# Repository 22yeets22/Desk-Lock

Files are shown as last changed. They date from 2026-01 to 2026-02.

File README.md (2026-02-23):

# Desk-Lock

A cheap desk lock that unlocks with an NFC card.

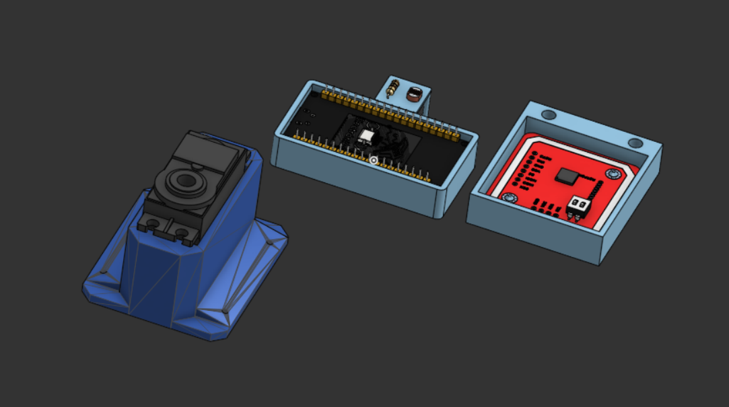
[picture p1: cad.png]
Desk Lock

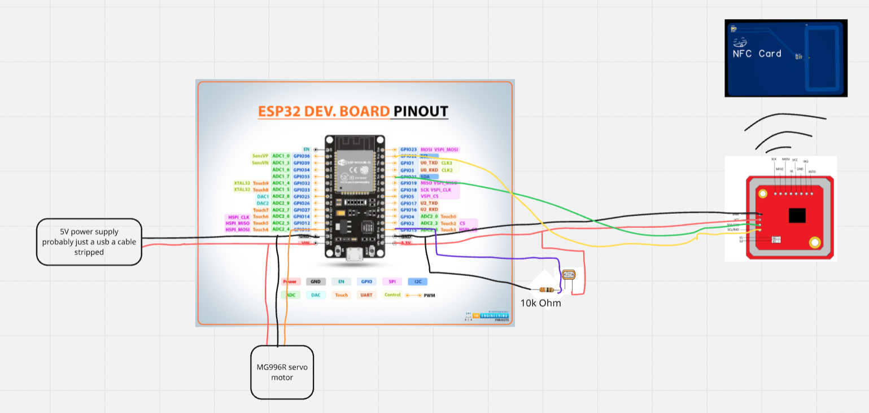
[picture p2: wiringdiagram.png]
Wiring Diagram


## Overview

This project is a DIY desk lock which keeps items in your desk secure by using a NFC reader. An ESP32 reads an NFC card via a PN532 module and controls a servo motor that locks or unlocks the desk. A photoresistor is used to detect when the drawer is closed so it can relock automatically.

[Detailed Description Here](#Detailed-Description)

## Motivation

I wanted a secure way to lock my desk because I keep important items inside and my little brother cannot be trusted with it. Buying a commercial lock felt boring and expensive, so building one with NFC was more interesting and let me design my own NFC card and reader.

## Parts List (Bill of Materials)

- 1x of [Photoresistor](https://www.aliexpress.us/item/3256805782399608.html), TYPE 5528, PRICE $2.39
- 1x of [10k Resistor](https://www.aliexpress.us/item/2251832766343175.html), TYPE 10K, PRICE $1.25
- 1x of [MG996R Servo](https://www.aliexpress.us/item/3256808293405785.html), TYPE N/A, PRICE $0.99
- 1x of [AC to DC Power Supply](https://www.aliexpress.us/item/3256806901002886.html), TYPE US Plug/DC 5V/4A, PRICE $4.60
- 1x of [ESP32 Development Board](https://www.aliexpress.us/item/3256805767190776.html), TYPE 1PCS-CP2102 TYPE-C, PRICE $6.56
- 1x of [PN532 NFC Module](https://www.aliexpress.us/item/3256806852006648.html), TYPE PN532, PRICE $3.67

### NFC Card - 25.33 for 5

| Schematic | PCB | 3D View |
| --- | --- | --- |
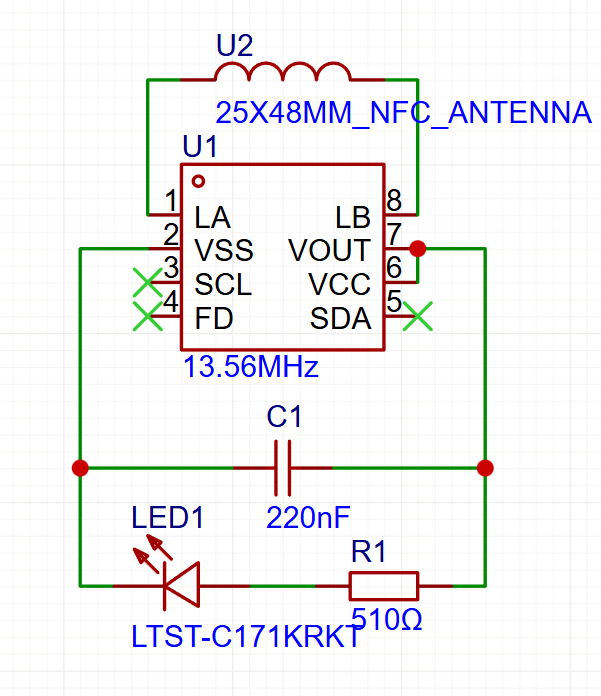
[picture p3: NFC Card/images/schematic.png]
Schematic
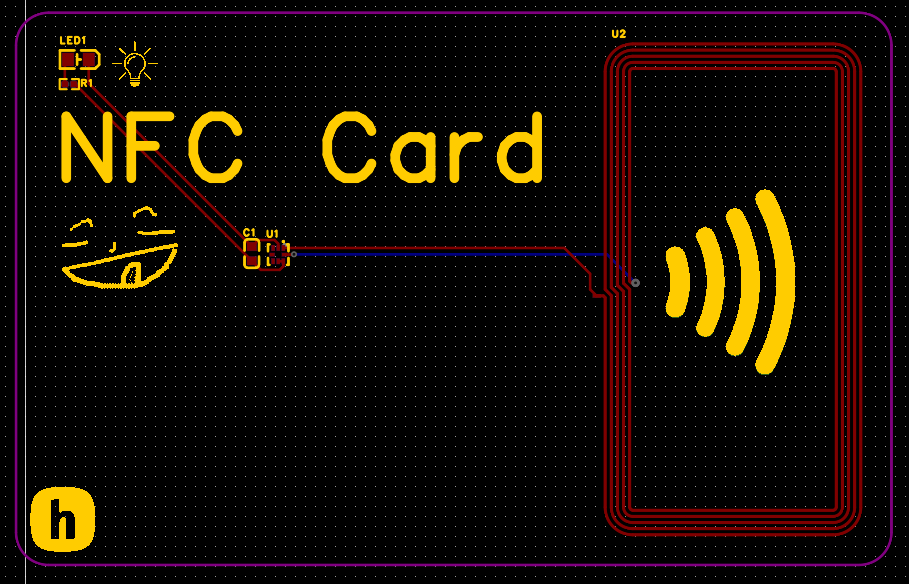
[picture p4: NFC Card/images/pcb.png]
PCB
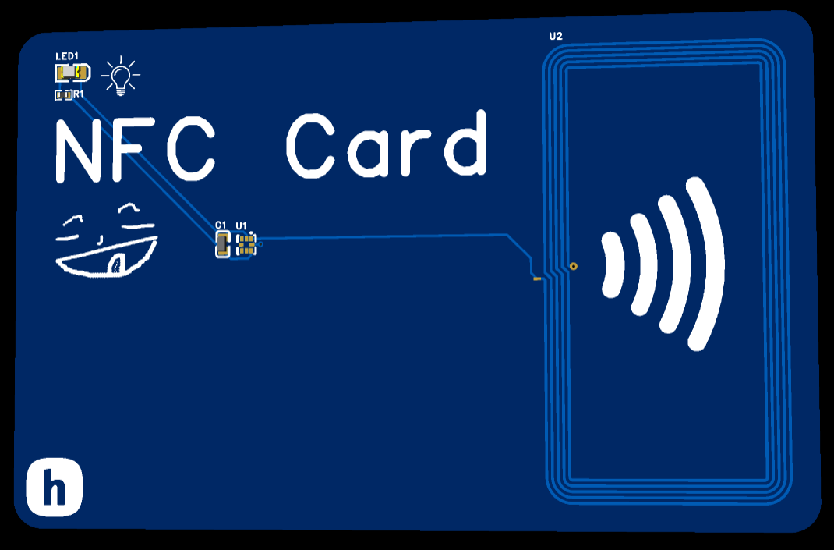
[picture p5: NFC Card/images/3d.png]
3D
|  |  |  |

## Detailed Description

This project is a DIY NFC-based desk lock using an ESP32. A PN532 NFC reader communicates with the ESP32 over I2C to read NFC cards. When an authorized card is detected, the ESP32 drives a servo motor to unlock the drawer. Unauthorized cards are ignored.<br>
The servo is powered by an external supply that also powers the ESP32 and is mounted so one position locks the drawer and another unlocks it. The mechanical design is flexible and can support different desk types.<br>
A photoresistor inside the drawer is wired as a voltage divider with a 10 kΩ resistor and connected to an ESP32 ADC pin. It detects whether the drawer is open or closed based on light level. After unlocking, the system waits until the drawer is closed (becomes dark), then automatically relocks after a configurable delay (default 10 seconds).

## CAD

There is a case for every single part in this project:

- ESP32 Case: for the esp32 (duh)
- PHotoresistor Case: for the photoresistor + resistor setup to detect desk drawer close
- MG996R Case: Servo case for a wider base which improves adhesion + screw holes if you need it
- PN532 Case (Case + Lid): Case + lid for the nfc reader module
- And also, a full assembly with all electronics included!

## Example Placement Diagram

Here is an example placement diagram for the servo:


## Notes

The servo holder was not made by me, but suits the purpose perfectly.

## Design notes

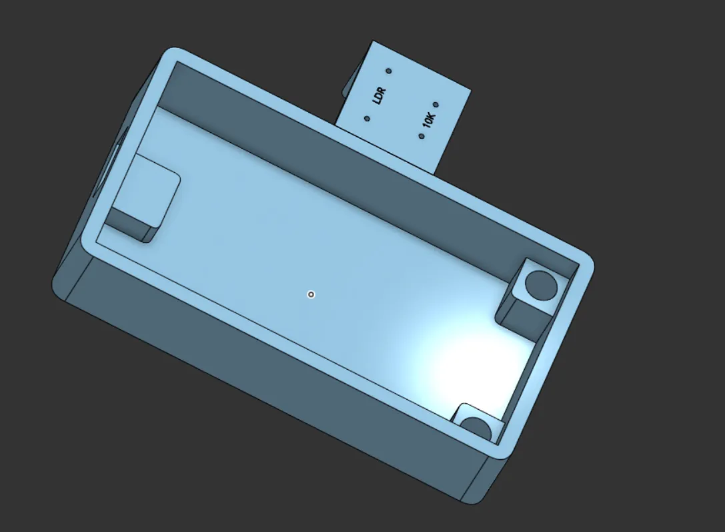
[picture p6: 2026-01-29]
3d.png

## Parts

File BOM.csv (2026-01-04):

Part | Type | Quantity | Unit Price | Link
Photoresistor | 5528 | 1 | 2.39 | https://www.aliexpress.com/item/3256805782399608.html
10k Resistor | 10K | 1 | 1.25 | https://www.aliexpress.com/item/2251832766343175.html
MG996R Servo | N/A | 1 | 0.99 | https://www.aliexpress.com/item/3256808293405785.html
AC to DC Power Supply | US Plug/DC 5V/4A | 1 | 4.60 | https://www.aliexpress.com/item/3256806901002886.html
ESP32 Dev Board | 1PCS-CP2102 TYPE-C | 1 | 6.56 | https://www.aliexpress.com/item/3256805767190776.html
PN532 NFC Module | PN532 | 1 | 3.67 | https://www.aliexpress.com/item/3256806852006648.html
CUSTOM NFC CARD | N/A | 5 | 25.33 | https://github.com/22yeets22/Desk-Lock/tree/main/NFC%20Card

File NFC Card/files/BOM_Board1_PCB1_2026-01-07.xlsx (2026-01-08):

No. | Quantity | Comment | Designator | Footprint | Value | Manufacturer Part | Manufacturer | Supplier Part | Supplier
1 | 1 | 220nF | C1 | C0603 | 220nF | CL10B224KA8NNNC | SAMSUNG(三星) | C21120 | LCSC
2 | 1 | LTST-C171KRKT | LED1 | LED-SMD_L2.0-W1.25-RD_RED |  | LTST-C171KRKT | LITEON(光宝) | C284871 | LCSC
3 | 1 | 510Ω | R1 | R0402 | 510Ω | RC0402FR-07510RL | YAGEO(国巨) | C276273 | LCSC
4 | 1 | 13.56MHz | U1 | XQFN-8_L1.6-W1.6-P0.50-BL_NT3H2111W0FHKH | 13.56MHz | NT3H2111W0FHKH | NXP(恩智浦) | C710403 | LCSC
5 | 1 | 25X48MM_NFC_ANTENNA | U2 | 25X48MM_NFC_ANTENNA

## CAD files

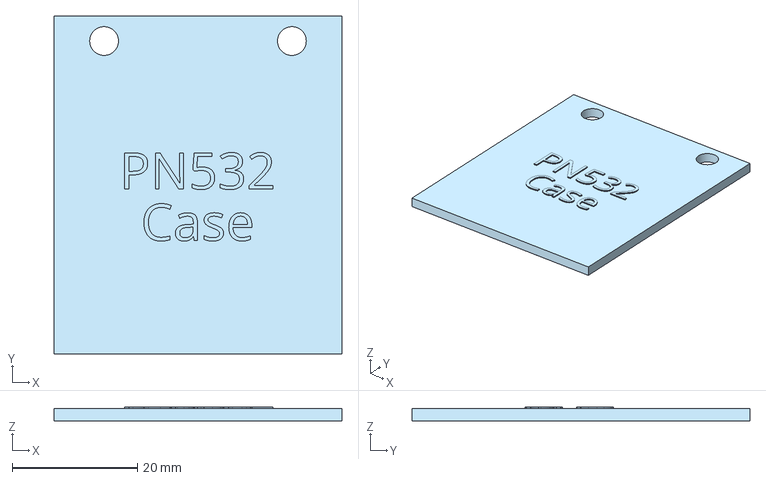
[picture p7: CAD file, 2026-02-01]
CAD/PN532 Case Lid.step
46.0 x 54.0 x 2.20 mm

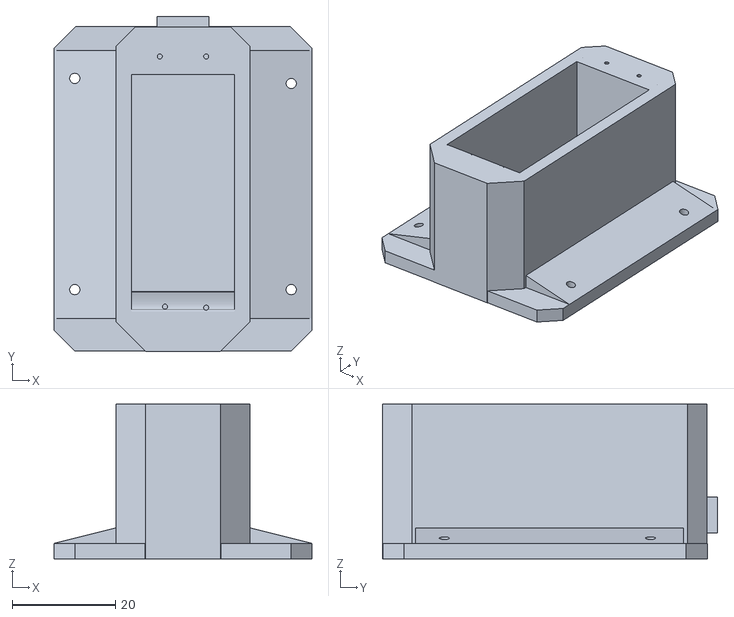
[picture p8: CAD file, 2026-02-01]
CAD/MG996R Case.stl
50.0 x 65.0 x 30.0

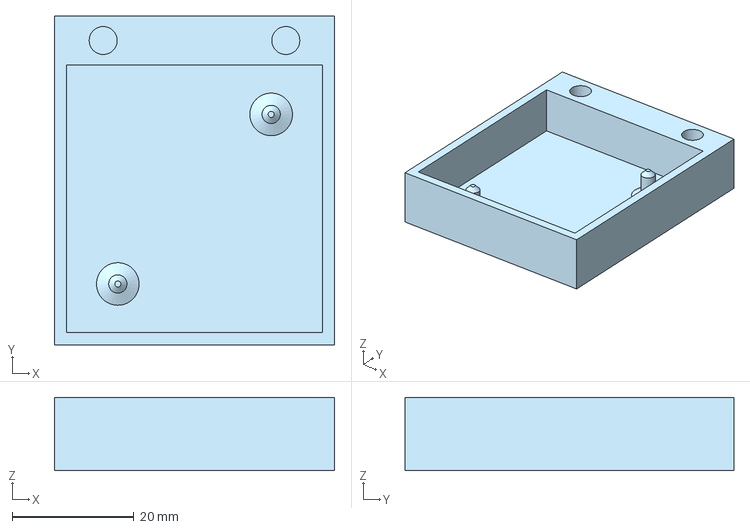
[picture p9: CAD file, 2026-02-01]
CAD/PN532 Case.step
46.0 x 54.0 x 12.0 mm

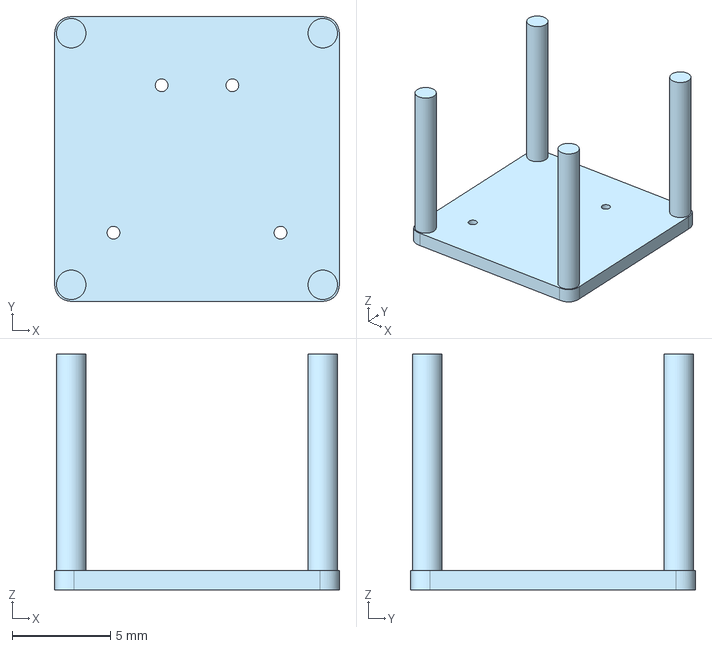
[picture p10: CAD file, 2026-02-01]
CAD/Photoresistor Case.step
14.5 x 14.5 x 12.0 mm

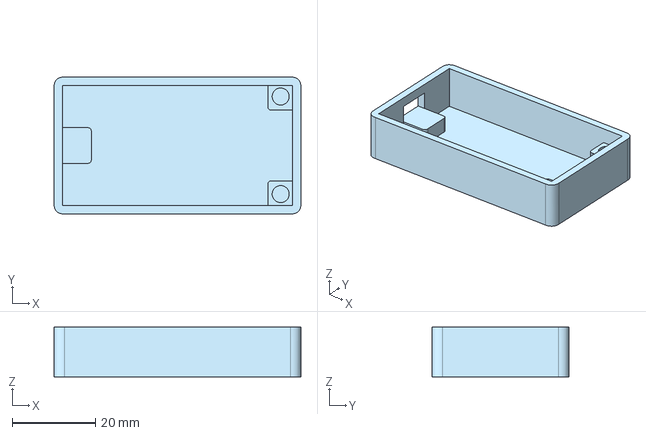
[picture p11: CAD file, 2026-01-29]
CAD/ESP32 Case.step
59.5 x 33.0 x 12.0 mm

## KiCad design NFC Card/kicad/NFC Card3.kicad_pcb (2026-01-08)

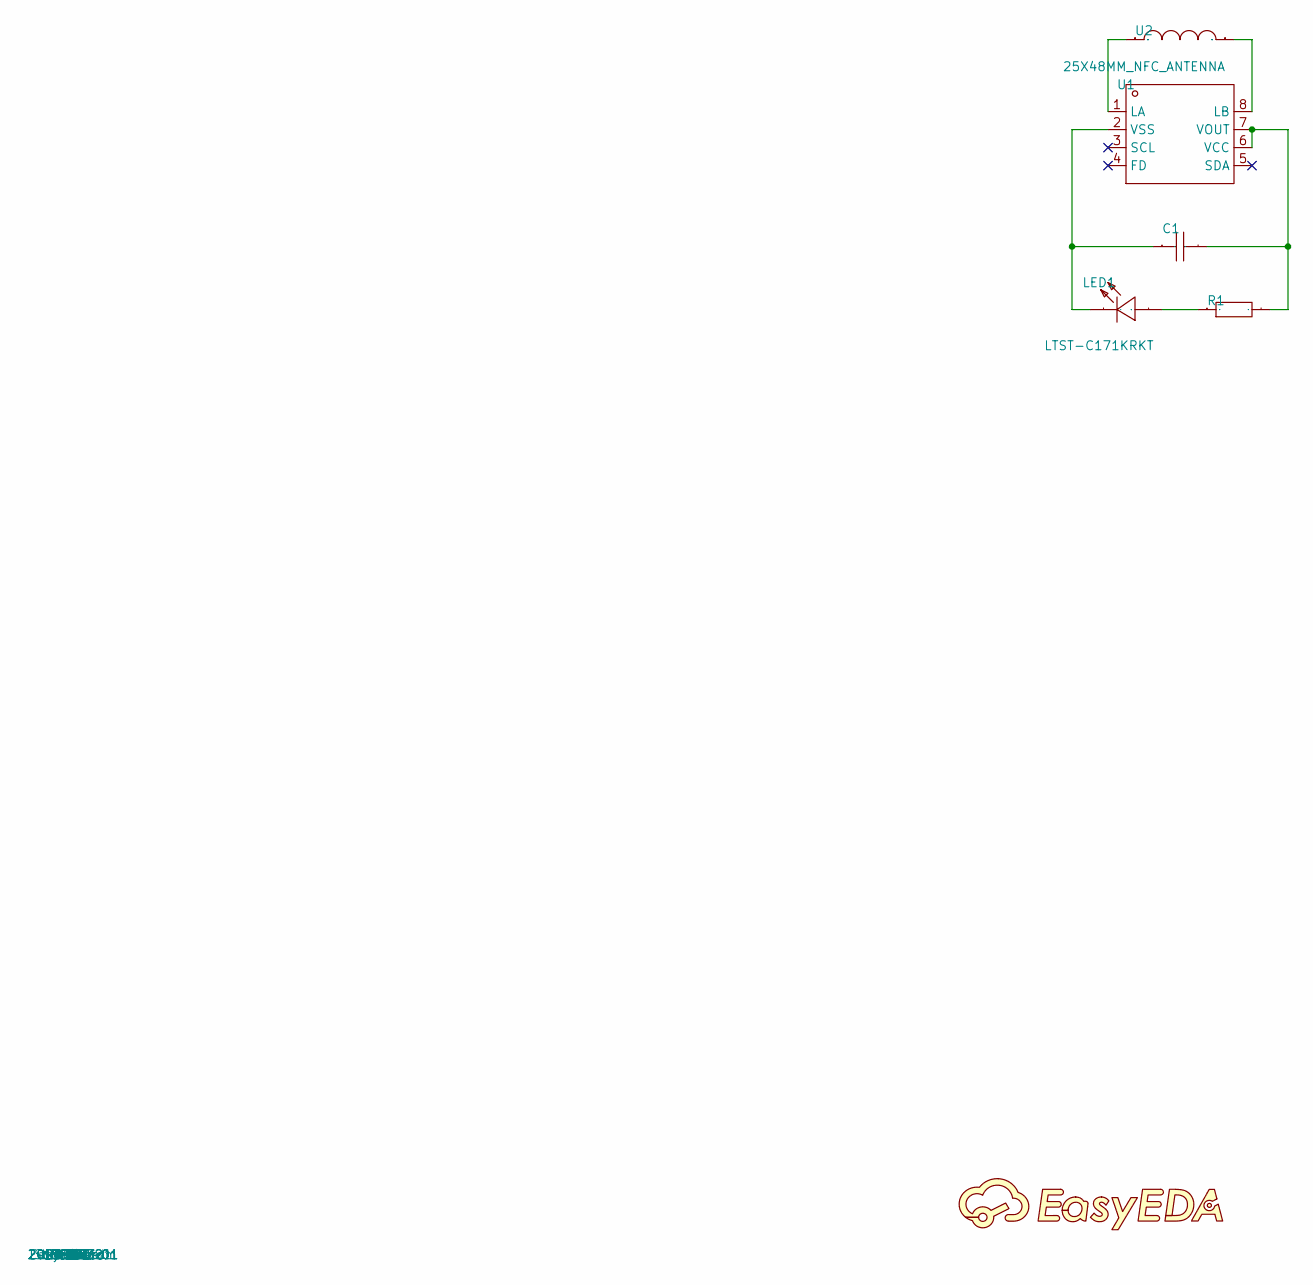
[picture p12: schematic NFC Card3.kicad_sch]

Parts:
C1: 220nF; C0603; Manufacturer Part CL10B224KA8NNNC; LCSC Part Name 220nF ±10% 25V
LED1: LTST-C171KRKT; LED-SMD_L2.0-W1.25-RD_RED; Manufacturer Part LTST-C171KRKT; LCSC Part Name 红灯
R1: 510Ω; R0402; Manufacturer Part RC0402FR-07510RL; LCSC Part Name 厚膜电阻 510Ω ±1% 62.5mW
U1: 13.56MHz; XQFN-8_L1.6-W1.6-P0.50-BL_NT3H2111W0FHKH; Manufacturer Part NT3H2111W0FHKH; LCSC Part Name NT3H2111W0FHKH
U2: 25X48MM_NFC_ANTENNA

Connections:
$1N430: U1.8 (LB), U2.P$2
$1N435: U1.1 (LA), U2.P$1
$1N518: C1.2, R1.2, U1.6 (VCC), U1.7 (VOUT)
$1N545: LED1.2 (A), R1.1
$1N550: C1.1, LED1.1 (C), U1.2 (VSS)

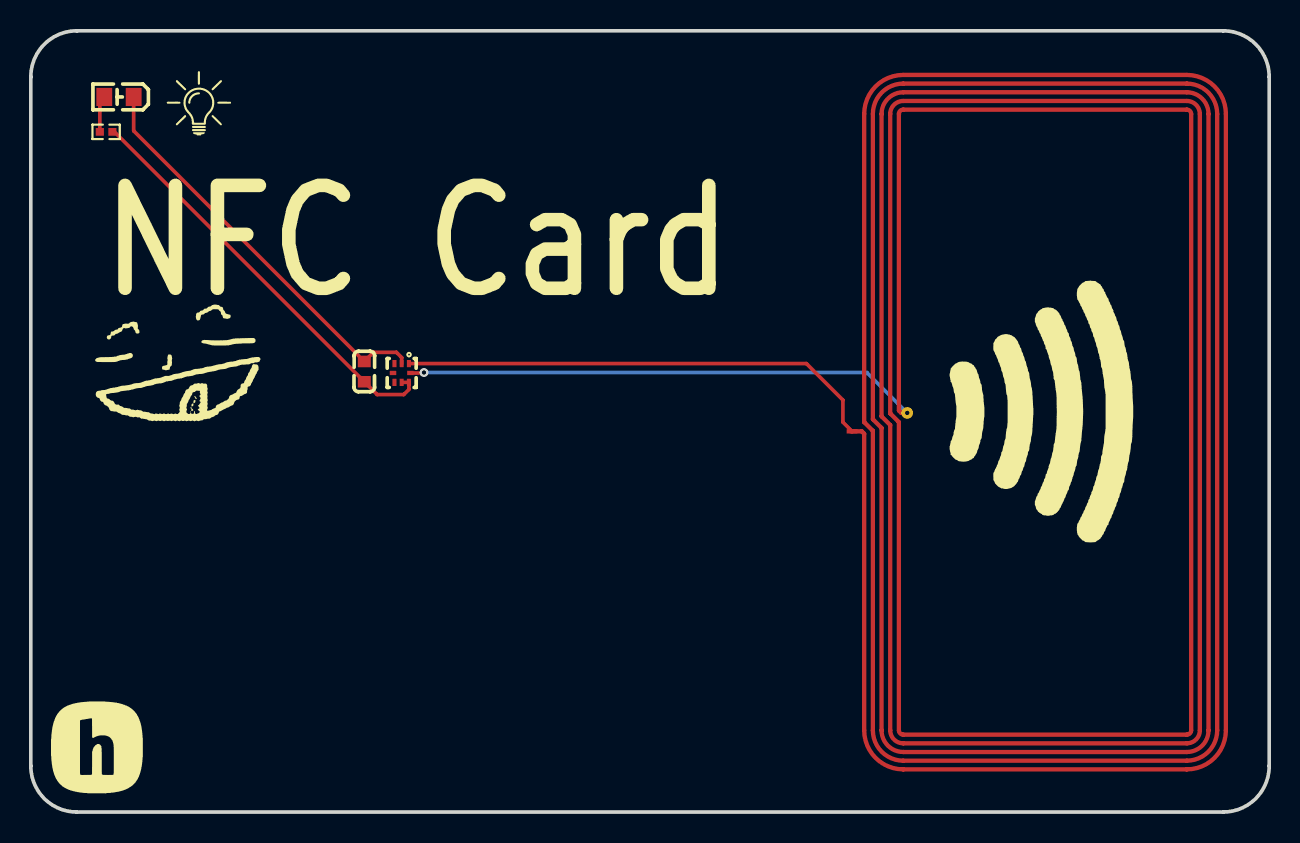
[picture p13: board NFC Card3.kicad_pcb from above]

Board: 2 copper layers, 85.6 x 54.0 mm, 5 parts (0 on the bottom side), 5 nets.

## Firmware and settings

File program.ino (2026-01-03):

#include <Wire.h>
#include <Adafruit_PN532.h>
#include <ESP32Servo.h>

// PIN DEFINITIONS
#define SDA_PIN 21  // pins for the pn532
#define SCL_PIN 22

#define PHOTO_PIN 15      // photoresistor analog input
#define SERVO_PIN 18      // servo control input

// CONSTANTS
const int POLL_EVERY = 2500;  // how often to poll the pn532
// lower = less energy but longer response time

Adafruit_PN532 nfc(SDA_PIN, SCL_PIN);

Servo lockServo;
const int SERVO_LOCKED = 20;     // adjust
const int SERVO_UNLOCKED = 90;  // adjust

const unsigned long DRAWER_CLOSE_TIME = 10000; // 10 seconds of dark before it closes

const int LIGHT_THRESHOLD = 1800;  // adjust too
// Above this = drawer open
// Below this = drawer closed

// AUTHORIZED UID
// Replace with your card UID
uint8_t allowedUID[] = {0xDE, 0xAD, 0xBE, 0xEF};
const uint8_t allowedUIDLength = 4;

// VARIABLES
bool drawerOpen = false;
unsigned long lightLowStart = 0;
bool lightTiming = false;


void setup() {
  Serial.begin(115200);

  // I2C
  Wire.begin(SDA_PIN, SCL_PIN);

  // Servo
  lockServo.attach(SERVO_PIN);
  lock();

  // NFC init
  nfc.begin();
  uint32_t versiondata = nfc.getFirmwareVersion();
  if (!versiondata) {
    Serial.println("PN532 not found");
    while (1) delay(1000);
  }

  nfc.setPassiveActivationRetries(0x00);  // try only once to read the card
  nfc.SAMConfig(); // configure to read rfid tags
  Serial.println("PN532 ready.");

  analogReadResolution(12);
}

void loop() {
  if (!drawerOpen) {
    wakePN532();
    checkNFC();
    sleepPN532();
    delay(POLL_EVERY);  // slow polling to reduce power
  } else {
    waitForDrawerClose();
  }
}

/* ================= FUNCTIONS ================= */

void sleepPN532() {
  // PN532 power‑down command
  uint8_t cmd[] = {0x16, 0x01};  
  if (nfc.sendCommandCheckAck(cmd, sizeof(cmd))) {
    Serial.println("PN532 powered down");
  } else {
    Serial.println("PowerDown failed");
  }
}

void wakePN532() {
  // simple wake by re‑begin
  nfc.begin();
  delay(10);  
  nfc.SAMConfig(); 
}

void checkNFC() {
  uint8_t uid[7];
  uint8_t uidLength;

  if (nfc.readPassiveTargetID(PN532_MIFARE_ISO14443A, uid, &uidLength)) {
    if (isAuthorized(uid, uidLength)) {
      Serial.println("Authorized card found!");
      unlock();
    } else {
      Serial.println("Unauthorized card.");
    }
  }
}

bool isAuthorized(uint8_t *uid, uint8_t uidLength) {
  if (uidLength != allowedUIDLength) return false;

  for (uint8_t i = 0; i < uidLength; i++) {
    if (uid[i] != allowedUID[i]) return false;
  }
  return true;
}

void waitForDrawerClose() {
  int lightValue = analogRead(PHOTO_PIN);

  if (lightValue < LIGHT_THRESHOLD) {
    if (!lightTiming) {
      lightTiming = true;
      lightLowStart = millis();
    }

    if (millis() - lightLowStart >= DRAWER_CLOSE_TIME) {
      Serial.println("Drawer confirmed closed. Locking.");
      lock();
      lightTiming = false;
    }
  } else {
    lightTiming = false;  // light came back, reset timer
  }

  delay(250);
}

void unlock() {
  lockServo.write(SERVO_UNLOCKED);
  drawerOpen = true;
}

void lock() {
  lockServo.write(SERVO_LOCKED);
  drawerOpen = false;
}

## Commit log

2026-01-03 Clarify comments for pin definitions and constants
    Updated comments for clarity on pin definitions and constants.
2026-01-03 add bom + motivation to readme
2026-01-04 Add BOM.csv with component details and pricing
    [BOM.csv]
2026-01-04 update .epro file,upload gerber and whatnot
    [BOM_Board1_PCB1_2026-01-04.xlsx, PickAndPlace_PCB1_2026-01-04.xlsx]
2026-01-04 Add CUSTOM NFC CARD entry to BOM.csv
    [BOM.csv]
2026-01-08 update ALL OF THE STINKIN NFC CARD FILES AND KICAD
    [BOM_Board1_PCB1_2026-01-04.xlsx, BOM_Board1_PCB1_2026-01-07.xlsx, NFC Card3.kicad_pcb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]
2026-01-29 added cad files + images + readme detailed desc
    [Desk Lock - Case.step, Desk Lock - Photoresistor.step]
2026-01-29 Update image file from cad.jpg to cad.png
2026-02-01 Update README with servo placement diagram
    Added an example placement diagram for the servo.
2026-02-01 new cad
    [Desk Lock - Photoresistor.step, ESP32.step, MG996R Holder.stl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]
2026-02-01 rename cad to be more specific
    [ESP32 Case.step, MG996R Case.stl, PN532 Case Lid.step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]
